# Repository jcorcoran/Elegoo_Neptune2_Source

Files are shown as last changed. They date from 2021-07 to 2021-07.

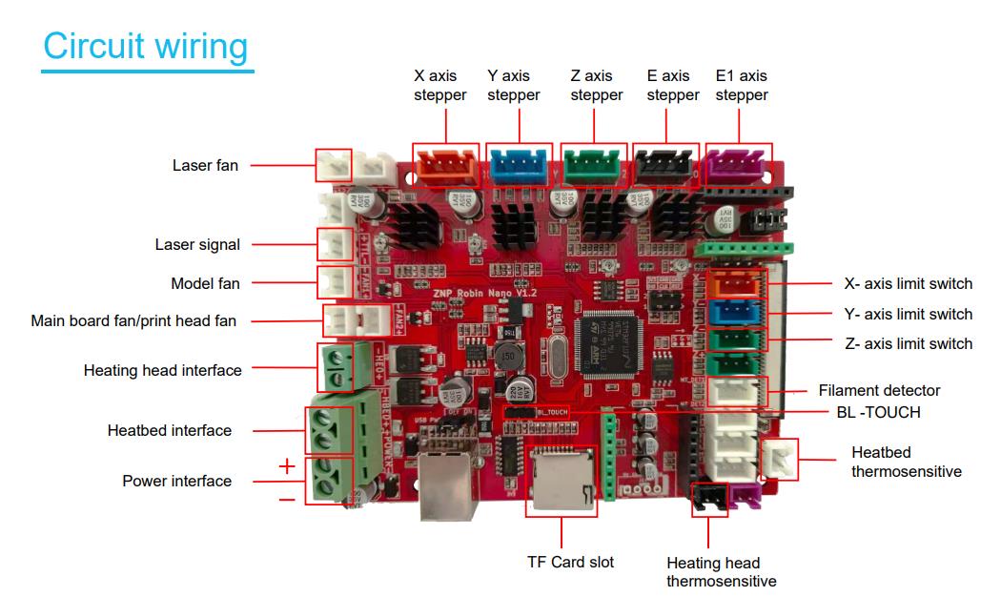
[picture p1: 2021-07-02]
PCBA/CIRCUIT WIRING.jpg

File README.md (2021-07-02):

# Elegoo_Neptune2_Source
Firmware, Shematics, BOM for the Elegoo Neptune2

This repo is a copy of the Elegoo Neptune 2 Source rar file hosted on the
[manufacturers web page](https://www.elegoo.com/pages/3d-printing-user-support) (downloaded 07/01/2021).  

Mirroring here for convenience of having the unpacked archive avaialble, and in the event it goes away/changes.

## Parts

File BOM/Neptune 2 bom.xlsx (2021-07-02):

Neptune 2 BOM
Order | Part Code | Part Name | Specification | UNIT | Qty
1 | 01.001.0001 | 2020 Aluminum profile_X-axis | 20*20-L345mm | pcs | 1.00
2 | 01.001.0002 | 2020 Aluminum profile_Top | 20*20-L330mm | pcs | 1.00
3 | 01.002.0001 | 2040 Aluminum profile_Right | 20*40-L400mm | pcs | 1.00
4 | 01.002.0002 | 2040 Aluminum profile_Left | 20*40-L400mm | pcs | 1.00
5 | 01.003.0001 | 4040 Aluminum profile_Y-axis | 40*40-L345mm | pcs | 1.00
6 | 01.003.0002 | 4040 Aluminum profile_Bottom & Right | 40*40-L290mm | pcs | 1.00
7 | 01.003.0003 | 4040 Aluminum profile_Bottom & Left | 40*40-L290mm | pcs | 1.00
8 | 01.003.0004 | 4040 Aluminum profile_Bottom | 40*40-L250mm | pcs | 1.00
9 | 02.001.0001 | Fixing Plate_Extruder | 2.5mm Aluminum alloy plate_AL5052 | pcs | 1.00
10 | 02.001.0002 | Fixing Plate_X-axis Motor | 3mm Aluminum alloy plate_AL5052 | pcs | 1.00
11 | 02.001.0003 | Driven Plate_X-axis | 2mm Aluminum alloy plate_AL5052 | pcs | 1.00
12 | 02.001.0001 | Driven Plate_Y-axis | SPCC t=2.0mm | pcs | 1.00
13 | 02.001.0004 | Fixing Plate_Y-axis Motor | 2.5mm Aluminum alloy plate_AL5052 | pcs | 1.00
14 | 02.001.0005 | Driven Plate_Z-axis | 3mm Aluminum alloy plate_AL5052 | pcs | 1.00
15 | 02.001.0006 | Fixing Plate_Nozzle Kit | 2.5mm Aluminum alloy plate_AL5052 | pcs | 1.00
16 | 02.001.0007 | Bottom Slider Plate | 4mm Aluminum alloy plate_AL5052 | pcs | 1.00
17 | 07.006.0001 | Thermistor_Heated Bed | D1.8mm_L700mm_100K | pcs | 1.00
18 | 07.006.0002 | Thermistor_Nozzle Kit | D1.8mm_L1300mm_100K | pcs | 1.00
19 | 07.007.0001 | Heating Tube | 24V_40W_L1400mm_Φ6mm*20mm | pcs | 1.00
20 | 07.005.0001 | 5015 Turbo Fan | 24V_5015_L120mm_Turbo Fan | pcs | 1.00
21 | 07.005.0002 | 4010 Turbo Fan | 24V_4010_L1310mm_Turbo Fan | pcs | 1.00
22 | 07.005.0003 | 4010 Axial Fan | 24V_4010_L1300mm_Axial Fan | pcs | 1.00
23 | 04.001.0001 | Yellew Earth Wire | 18AWG_L170mm_4.0 U-terminal+4.8 Plug spring terminal | pcs | 1.00
24 | 04.001.0002 | Black Silicone Wire | 16AWG_L170mm_4.0 U-terminal+4.8 Plug spring terminal | pcs | 1.00
25 | 04.002.0001 | Heated Bed Wire | 16AWG_L600mm_Strip 6mm at both ends and add tin | pcs | 1.00
26 | 04.001.0003 | Red Silicone Wire_Combined Switch | 16AWG_L90mm_4.8 Plug spring terminal(Both sides) | pcs | 1.00
27 | 04.003.0001 | Red And Black Wire_Mainboard | 16AWG_L410mm_Amass XT60 female terminal+Strip 5mm and add tin | pcs | 1.00
28 | 04.004.0001 | Red And Black Wire_Power Supply | 16AWG-L200mm_Amass XT60 male terminal+4.0 U-terminal | pcs | 1.00
29 | 04.005.0001 | Motor and limit switch wire_Y-axis | L380mm | pcs | 1.00
30 | 04.005.0002 | Motor and limit switch wire_Z-axis | Motor-L250mm_Limit switch-L290mm | pcs | 1.00
31 | 04.001.0004 | Red Silicone Wire_Combined Switch | 16AWG_L170mm_4.0 U-terminal+4.8 Plug spring terminal | pcs | 1.00
32 | 04.005.0003 | Motor and limit switch wire_X/E-axis | E-axis Motor-L810mm_X-axis Motor-L860mm_X-axis limit switch-L910mm | pcs | 1.00
33 | 04.006.0001 | Filament Detector Wire | L880mm | pcs | 1.00
34 | 05.001.0001 | Plastic Bottom Box | Black_ABS765A Fireproof materials_Fire ratingV-0 | pcs | 1.00
35 | 05.001.0002 | Plastic Bottom Cover | Black_ABS765A Fireproof materials_Fire ratingV-0 | pcs | 1.00
36 | 05.001.0003 | Screen Fixing Bracket | Black_ABS765A Fireproof materials_Fire ratingV-0 | pcs | 1.00
37 | 05.001.0004 | Fan Cover | Black_ABS765A Fireproof materials_Fire ratingV-0 | pcs | 1.00
38 | 05.001.0005 | Power Supply Fixing Box | Black_ABS765A Fireproof materials_Fire ratingV-0 | pcs | 1.00
39 | 05.001.0006 | Fixed Seat_Heated Bed Wire | Black_ABS765A Fireproof materials_Fire ratingV-0 | pcs | 1.00
40 | 05.001.0007 | Fixed Seat Cover_Heated Bed Wire | Black_ABS765A Fireproof materials_Fire ratingV-0 | pcs | 1.00
41 | 05.001.0008 | Fixed Seat_Filament Detector Switch | Black_ABS765A Fireproof materials_Fire ratingV-0 | pcs | 1.00
42 | 05.001.0009 | Extruder Base | Black_ABS765A+PC Fireproof materials_Fire ratingV-0 | pcs | 1.00
43 | 05.001.0010 | Extruder Handle | Black_ABS765A+PC Fireproof materials_Fire ratingV-0 | pcs | 1.00
44 | 05.001.0011 | Fixed Seat of Limit Switch_X-axis | Black_ABS765A Fireproof materials_Fire ratingV-0 | pcs | 1.00
45 | 05.001.0012 | Fixed Seat of Limit Switch_Z-axis | Black_ABS765A Fireproof materials_Fire ratingV-0 | pcs | 1.00
46 | 05.001.0015 | Fixed Seat of Limit Switch_Y-axis | Black_ABS765A Fireproof materials_Fire ratingV-0 | pcs | 1.00
47 | 05.001.0014 | Filament Holder | Black_ABS765A Fireproof materials_Fire ratingV-0 | pcs | 1.00
48 | 05.001.0015 | Filament Tube | Black_ABS765A+PC Fireproof materials_Fire ratingV-0 | pcs | 1.00
49 | 05.001.0016 | 4040 Profile Cover | Black_ABS765A Fireproof materials_Fire ratingV-0 | pcs | 4.00
50 | 05.001.0017 | 2020 Profile Cover | Black_ABS765A Fireproof materials_Fire ratingV-0 | pcs | 2.00
51 | 05.001.0018 | Hand Screw Nut | Black_ABS765A Fireproof materials_Fire ratingV-0 | pcs | 4.00
52 | 05.001.0019 | Fixed Seat of Stepper_Z-axis | Black_ABS765A Fireproof materials_Fire ratingV-0 | pcs | 1.00
53 | 05.001.0020 | Silicone Cover | Silica Gel_Black | pcs | 1.00
54 | 05.001.0021 | Clamp of Pneumatic Fittings | φ5.7mm Blue | pcs | 3.00
55 | 08.001.0001 | Neptune 2 Mainboard | Elegoo ZNP Robin Nano V1.2 | pcs | 1.00
56 | 08.002.0001 | Neptune 2 Display Screen | Elegoo ZNP Robin TFT35 V1.0 | pcs | 1.00
57 | 04.007.0001 | FFC Cable | FFC Cable_L300mm_32P_Distance 1.0mm_Same side | pcs | 1.00
58 | 07.003.0001 | Limit Switch | With PCBA | pcs | 3.00
59 | 07.003.0002 | Filament Detector Switch | With PCBA | pcs | 1.00
60 | 07.002.0004 | 42-34 Stepper_Black（Flat shaft） | 42HD2037-02_Two-phase_Black | pcs | 2.00
61 | 07.002.0005 | 42-34 Stepper_Black（Circular Axis） | 42HD2037-04_Two-phase_Black | pcs | 1.00
62 | 07.002.0006 | 42-40 Stepper_Black | 42HD4027-02_Two-phase_Black | pcs | 1.00
63 | 07.001.0001 | Power Supply_Black | 24V_15A | pcs | 1.00
64 | 07.003.0003 | Combination Switch | Three-in-one combination switch | pcs | 1.00
65 | 08.003.0001 | Fuse | 10A_250V_5mm*20mm | pcs | 1.00
66 | 07.004.0001 | Heated Bed Platform | 24V_235mm*235mm_220W | pcs | 1.00
67 | 03.002.0001 | Heating Block | 20mm*20mm*10mm | pcs | 1.00
68 | 03.003.0001 | Heat Dissipation Block | 12mm*20mm*27.8mm_2*M3 | pcs | 1.00
69 | 03.004.0001 | Nozzle | 0.4mm | pcs | 2.00
70 | 03.005.0001 | Throat Tube | D7mm_M6_L27mm_through | pcs | 1.00
71 | 03.007.0001 | V-slot Wheel | Black_Imported POM_Size：24*10mm | pcs | 13.00
72 | 03.006.0001 | Metal Eccentric Spacer | D7.2mm_d5mm_H8.35mm_Outer Hexagon | pcs | 5.00
73 | 03.006.0002 | Metal Spacer | D8mm_d5mm_H8.35mm | pcs | 11.00
74 | 03.001.0001 | Extrusion Gear | D11mm_40teeth_Copper | pcs | 1.00
75 | 06.004.0001 | Compression Spring_Heated Bed | φ0.9mm*φ8mm*L20mm | pcs | 4.00
76 | 06.004.0002 | Compression Spring_Nozzle Kit | φ1.1mm*φ8mm*L22mm | pcs | 1.00
77 | 06.001.0001 | Ball bearing_U-624 | U-624 | pcs | 1.00
78 | 06.001.0002 | Ball bearing_F-624-ZZ | F-624-ZZ | pcs | 4.00
79 | 06.001.0003 | Ball bearing_625-ZZ | 625-ZZ | pcs | 26.00
80 | 06.003.0001 | Lead Screws_T8 | T8-8_L355mm | pcs | 1.00
81 | 06.003.0002 | Lead Screws Nut_T8 | T8-8 | pcs | 1.00
82 | 06.007.0001 | Rigid Coupling | D5mm*8mm | pcs | 1.00
83 | 06.009.0001 | Pneumatic Fittings | PC4-1/8PT | pcs | 3.00
84 | 06.006.0001 | Timing Pulley | 2GT_d5mm_20teeth_W6mm | pcs | 2.00
85 | 05.002.0001 | Timing Belt | 2GT-W6_X-axis 780mm_Y-axis 750mm | m | 1.53
86 | 06.009.0002 | Copper Sleeve_Timing Belt | D7mm_0.5mm | pcs | 4.00
87 | 05.003.0001 | Nylon Column Ⅰ | φ7mm-φ4.2mm-H15mm | pcs | 2.00
88 | 05.003.0002 | Nylon Column Ⅱ | φ7mm-φ4.2mm-H8mm | pcs | 2.00
89 | 10.006.0001 | Platform Sticker | 235mm*235mm | pcs | 1.00
90 | 05.006.0001 | Glass Fiber Platform | 235mm*235mm | pcs | 1.00
91 | 10.005.0001 | Rubber Mat | 20*40mm_H3mm | pcs | 4.00
92 | 05.007.0001 | Teflon Tube | D4-d2_white_L380mm | m | 0.38
93 | 10.001.0001 | Nylon braided sleeve Ⅰ | W8mm_L410mm | pcs | 1.00
94 | 10.001.0004 | Nylon braided sleeve Ⅱ | W8mm_L700mm | pcs | 1.00
95 | 10.001.0003 | Nylon braided sleeve Ⅲ | W12mm_L650mm | pcs | 1.00
96 | 11.003.0001 | Insulation Cotton | 50mm*60mm | pcs | 1.00
97 | 10.008.0001 | Long Tail Clip | 6#_15mm | pcs | 4.00
98 | 10.007.0004 | Cable Tie 4-150 | Black_4*150mm | pcs | 15.00
99 | 10.007.0005 | Fixed Head Cable Tie 3-100 | Black_3*100mm | pcs | 2.00
100 | 11.002.0003 | High Temperature Insulating Polyimide Tape Ⅰ | W10mm | m | 0.08
101 | 11.002.0002 | High Temperature Insulating Polyimide Tape Ⅱ | W50mm | m | 0.20
102 | 11.001.0001 | High Temp Resistant Thread Sealant | 272_Red_High Temp Resistant | g | 0.50
103 | 11.004.0001 | Grease | Transparent_Paste | g | 2.00
104 | 11.004.0002 | Thermal Grease | Grey | g | 0.20
105 | 10.004.0001 | TF Memory Card | 8G | pcs | 1.00
106 | 10.004.0002 | TF Memory Card Reader | CHUANYU（Common） | pcs | 1.00
107 | 04.008.0005 | Power Supply | Length:1.5M_Wire diameter:6.5mm_Rated power:2500W_Rated voltage:250V_Pure copper_3*0.75mm²_Plug:nickel-plated brass_Flame-Retardant PVC | pcs | 1.00
108 | 04.009.0001 | USB Cable | Bluish transparent_Type-A to Type-B_Length:53cm_Wire diameter:4.8mm | pcs | 1.00
109 | 10.008.0002 | Needle | Stainless Steel_L70mm_d0.35mm | pcs | 1.00
110 | 10.002.0001 | Metal Scraper | Stainless Steel_1.5#_Nickel-plated | pcs | 1.00
111 | 10.002.0002 | Nippers | Cutting Nippers | pcs | 1.00
112 | 10.002.0003 | 1.5mm Inner Hexagon Spanner | Carbon Steel_1.5mm_Nickel-plated | pcs | 1.00
113 | 10.002.0004 | 2.0mm Inner Hexagon Spanner | Carbon Steel_2.0mm_Nickel-plated | pcs | 1.00
114 | 10.002.0005 | 2.5mm Inner Hexagon Spanner | Carbon Steel_2.5mm_Nickel-plated | pcs | 1.00
115 | 10.002.0006 | 3.0mm Inner Hexagon Spanner | Carbon Steel_3.0mm_Nickel-plated | pcs | 1.00
116 | 10.002.0007 | 4.0mm Inner Hexagon Spanner | Carbon Steel_4.0mm_Nickel-plated | pcs | 1.00
117 | 10.002.0008 | Flat Blade Screwdriver | 2.5mm_Flat Blade | pcs | 1.00
118 | 10.002.0009 | Cruciform Screwdriver | 4.0mm_ Cruciform | pcs | 1.00
119 | 10.002.0010 | Double Open Spanner | 45#steel_8-10#_Galvanized | pcs | 1.00
120 | 10.002.0011 | Open Spanner | 45#steel_6#_Galvanized | pcs | 1.00
121 | 12.002.0005 | Lead Screws Sleeve | PE_30mm*370mm_Single side Thickness:0.1mm | pcs | 1.00
122 | 12.002.0001 | Self Sealing Bag Ⅰ | 18cm*26cm_Thickness:0.06mm | pcs | 1.00
123 | 12.002.0002 | Self Sealing Bag Ⅱ | 15cm*20cm_Thickness:0.08mm | pcs | 2.00
124 | 12.002.0003 | Self Sealing Bag Ⅲ | 9cm*13cm_Thickness:0.08mm | pcs | 3.00
125 | 12.002.0004 | Self Sealing Bag Ⅳ | 6cm*9cm_Thickness:0.08mm | pcs | 2.00
126 | 13.001.0001 | Filament | L5m_Random color | pcs | 1.00
127 | 10.003.0001 | Product Certificate | Triangle | pcs | 1.00
128 | 12.003.0001 | Neptune 2 Foam |  | pcs | 1.00
129 | 12.001.0001 | Neptune 2 Carton |  | pcs | 1.00
130 | 10.003.0003 | Neptune 2 User Guide |  | pcs | 1.00
131 | 12.004.0001 | Neptune 2 Manufacturing Number Sticker |  | pcs | 1.00
132 | 12.004.0002 | Neptune 2 Machine Specification Sticker |  | pcs | 1.00
133 | 10.007.0003 | Plastic Twist Tie | White_Plastic Twist Tie_0.55mm*80mm | pcs | 1.00
134 | 12.005.0001 | Heated Bed Warning Sticker | 80G_Coated Paper | pcs | 1.00
135 | 09.001.0001 | Hexagon Socket Countersunk Head Screw_M3*18 | Stainless Steel_M3*18 | pcs | 4.00
136 | 09.001.0002 | Hexagon Socket Countersunk Head Screw_M3*10 | Stainless Steel_M3*10 | pcs | 1.00
137 | 09.001.0003 | Hexagon Socket Countersunk Head Screw_M4*20 | Carbon Steel_M4*20 | pcs | 2.00
138 | 09.001.0004 | Cross Recessed Countersunk Head Screw_M4*35 | Stainless Steel_M4*35 | pcs | 4.00
139 | 09.002.0001 | Hexagon Socket Button Head Screw_M3*6 | Stainless Steel_M3*6 | pcs | 12.00
140 | 09.002.0002 | Hexagon Socket Button Head Screw_M3*16 | Stainless Steel_M3*16 | pcs | 4.00
141 | 09.002.0003 | Hexagon Socket Button Head Screw_M5*30 | Stainless Steel_M5*30 | pcs | 10.00
142 | 09.002.0004 | Hexagon Socket Button Head Screw_M3*10 | Stainless Steel_M3*10 | pcs | 4.00
143 | 09.002.0005 | Hexagon Socket Button Head Screw_M5*40 | Stainless Steel_M5*40 | pcs | 3.00
144 | 09.002.0006 | Hexagon Socket Button Head Screw_M5*8 | Stainless Steel_M5*8 | pcs | 4.00
145 | 09.002.0007 | Hexagon Socket Button Head Screw_M4*16 | Stainless Steel_M4*16 | pcs | 6.00
146 | 09.002.0008 | Hexagon Socket Button Head Screw_M4*6 | Carbon Steel_M4*6 | pcs | 1.00
147 | 09.002.0009 | Hexagon Socket Button Head Screw_M3*12 | Stainless Steel_M3*12 | pcs | 2.00
148 | 09.003.0001 | Hexagon Socket Head Cap Screw_M4*8 | Stainless Steel_M4*8 | pcs | 10.00
149 | 09.003.0002 | Hexagon Socket Head Cap Screw_M3*18 | Stainless Steel_M3*18 | pcs | 1.00
150 | 09.003.0003 | Hexagon Socket Head Cap Screw_M4*35 | Stainless Steel_M4*35 | pcs | 1.00
151 | 09.003.0004 | Hexagon Socket Head Cap Screw_M4*18 | Stainless Steel_M4*18 | pcs | 2.00
152 | 09.003.0005 | Hexagon Socket Head Cap Screw_M4*20 | Stainless Steel_M4*20 | pcs | 2.00
153 | 09.003.0006 | Hexagon Socket Head Cap Screw_M4*50 | Stainless Steel_M4*50 | pcs | 1.00
154 | 09.003.0007 | Hexagon Socket Head Cap Screw_M4*10 | Stainless Steel_M4*10 | pcs | 2.00
155 | 09.004.0001 | M5 Flat Washer_V-slot Wheel | M5_φ5mm*φ8mm*1mm | pcs | 13.00
156 | 09.004.0002 | M3 Spring Washer | Stainless Steel_M3 | pcs | 4.00
157 | 09.004.0003 | M5 Flat Washer | Stainless Steel_M5 | pcs | 5.00
158 | 09.004.0004 | M4 Spring Washer | Stainless Steel_M4 | pcs | 2.00
159 | 09.005.0001 | M4 T-nut | Stainless Steel_M4 | pcs | 8.00
160 | 09.005.0002 | M5 Self-locking Nut | Stainless Steel_M5 | pcs | 13.00
161 | 09.005.0003 | 4 Self-locking Nut | Stainless Steel_M4 | pcs | 1.00
162 | 09.005.0004 | Self-locking Nut | Stainless Steel_M3 | pcs | 2.00
163 | 09.006.0001 | Pan Head Tapping Screws_Point Tail_3*14 | Stainless Steel_PA 3*14 | pcs | 2.00
164 | 09.006.0002 | Pan Head Tapping Screws_Point Tail_3*12 | Stainless Steel_PA 3*12 | pcs | 8.00
165 | 09.006.0003 | Pan Head Tapping Screws_Point Tail_3*8 | Stainless Steel_PA 3*8 | pcs | 15.00
166 | 09.006.0004 | Pan Head Tapping Screws_Point Tail_3*20 | Stainless Steel_PA 3*20 | pcs | 2.00
167 | 09.007.0001 | Combination Screw_M3*4 | Stainless Steel_M3*4 | pcs | 1.00
168 | 09.007.0002 | Combination Screw with Spring washer_M4*18 | Carbon Steel_M4*18 | pcs | 4.00
169 | 09.007.0003 | Combination Screw with Spring washer_M5*25 | Carbon Steel_M5*25 | pcs | 4.00
170 | 09.007.0004 | Combination Screw with Spring washer_M5*45 | Carbon Steel_M5*45 | pcs | 10.00
171 | 09.008.0001 | Set Screw_M3*3 | Carbon Steel_M3*3 | pcs | 4.00

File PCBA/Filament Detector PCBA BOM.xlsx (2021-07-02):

序号 | 名称 | 规格 | 数量 | 单位
1 | PCB |  | 1 | pcs
2 | 贴片电容 | 100nF | 2 | pcs
3 | 贴片电阻 | 0Ω | 1 | pcs
4 | 贴片电阻 | 510Ω | 1 | pcs
5 | 发光二极管 0603 | 蓝色 | 1 | pcs
6 | 微动开关 |  | 1 | pcs
7 | 接线端子 | 2.54-3P | 1 | pcs

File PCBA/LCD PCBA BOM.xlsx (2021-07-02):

序号 | 名称 | 规格 | 数量 | 单位
1 | PCB |  | 1 | pcs
2 | 贴片电容 | 100nF | 4 | pcs
3 | 贴片电容 | 10nF | 2 | pcs
4 | 贴片电容 | 4.7uF | 2 | pcs
5 | 贴片电阻 | 1KΩ | 4 | pcs
6 | 贴片电阻 | 10KΩ | 3 | pcs
7 | 集成电阻 | 47Ω | 1 | pcs
8 | IC TSC2046I | TSSOP-16 | 1 | pcs
9 | 蜂鸣器 |  | 1 | pcs
10 | 三极管 | BC817 | 1 | pcs
11 | 三极管 | BCW66 | 1 | pcs
12 | 贴片连接器下接 | FPC-32pin-1.0mm | 1 | pcs
13 | 贴片连接器抽屉上接 | FPC-40pin-0.5mm | 1 | pcs
14 | 显示屏带触摸屏 |  | 1 | pcs
15 | 显示屏框 | 3.5吋黑色 | 1 | pcs

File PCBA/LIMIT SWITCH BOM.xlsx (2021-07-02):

序号 | 名称 | 规格 | 数量 | 单位
1 | PCB |  | 1 | pcs
2 | 微动开关 |  | 1 | pcs
3 | 接线端子 | 2.54-3P | 1 | pcs
4 | 盘头自攻螺丝 |  | 2 | pcs

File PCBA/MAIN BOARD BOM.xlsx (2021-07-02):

序号 | 名称 | 规格 | 数量 | 单位
1 | PCB |  | 1 | pcs
2 | C0603 | 100nF | 41 | pcs
3 | C0603 | 22pF | 2 | pcs
4 | C0603 | 22nF | 2 | pcs
5 | C0603 | 220nF | 2 | pcs
6 | C0603 | 150pF | 1 | pcs
7 | C0603 | 1uF | 1 | pcs
8 | C0805 | 10uF | 2 | pcs
9 | 贴片铝电解电容 | 10uF | 3 | pcs
10 | 贴片铝电解电容 | 100uF | 7 | pcs
11 | 贴片铝电解电容 | 220uF | 1 | pcs
12 | 电阻0603 | 4.7KΩ | 18 | pcs
13 | 电阻0603 | 10KΩ | 18 | pcs
14 | 电阻0603 | 0Ω | 10 | pcs
15 | 电阻0603 | 1KΩ | 10 | pcs
16 | 电阻0603 | 20KΩ | 10 | pcs
17 | 电阻0603 | 100Ω | 5 | pcs
18 | 电阻0603 | 100KΩ | 4 | pcs
19 | 电阻0603 | 22Ω | 2 | pcs
20 | 电阻0603 | 1MΩ | 1 | pcs
21 | 电阻0603 | 210KΩ | 1 | pcs
22 | 电阻0603 | 40.2KΩ | 1 | pcs
23 | 电阻0603 | 24.9K | 1 | pcs
24 | 电阻0603 | 1.8KΩ | 3 | pcs
25 | 电阻0805 | 0.11Ω | 4 | pcs
26 | 电阻0805 | 0.1Ω | 4 | pcs
27 | 电阻0805 | 10Ω | 1 | pcs
28 | 可调电位器 | 20KΩ | 2 | pcs
29 | 贴片电感 | 15uH | 1 | pcs
30 | L0805 | BLM21PG221SN1D | 1 | pcs
31 | 整流二级管 | S1G | 1 | pcs
32 | 整流二级管 | S1A | 1 | pcs
33 | 二极管 | B340A | 1 | pcs
34 | 整流二极管 | SS12A | 1 | pcs
35 | 发光二极管 0603 | 红色 | 5 | pcs
36 | 发光二极管 0603 | 绿色 | 2 | pcs
37 | TMC2225 | TMC2225 | 2 | pcs
38 | STM32F103VET6 | LQFP100 | 1 | pcs
39 | A4988 | A4988 | 2 | pcs
40 | IC AT24C16N | SOIC-8 | 1 | pcs
41 | IC MP1584EN | SOIC-8 | 1 | pcs
42 | IC CH340C | SOP | 1 | pcs
43 | IC NCP1117ST33T3G | SOT | 1 | pcs
44 | IC W25Q64JVSSIQ | SOIC | 1 | pcs
45 | 晶振8M-20pF | DIP | 1 | pcs
46 | 保险丝-3216FF | 30A | 1 | pcs
47 | 保险丝-3216FF | 15A | 1 | pcs
48 | 自恢复保险丝 | MSMD15 | 1 | pcs
49 | 自恢复保险丝 | MSMD050 | 1 | pcs
50 | 贴片连接器下接 | FPC-32pin-1.0mm | 1 | pcs
51 | Micro SD镀金卡座 |  | 1 | pcs
52 | 集成电阻 | 100Ω | 5 | pcs
53 | 集成电阻 | 10Ω | 1 | pcs
54 | 集成电阻 | 4.7KΩ | 1 | pcs
55 | 集成电阻 | 100KΩ | 1 | pcs
56 | 压敏电阻 | 05E | 3 | pcs
57 | NMOS管 | AO3400 | 2 | pcs
58 | 贴片可调电位器 | 10KΩ | 2 | pcs
59 | MOS管 | HY1403D | 1 | pcs
60 | MOS管 | HY3403D | 1 | pcs
61 | 插座 2.54 | M8x1黑色 | 2 | pcs
62 | 插座 2.54 | M8x1绿色 | 2 | pcs
63 | 螺钉式接线端子 5.0-2P | 绿色 | 1 | pcs
64 | 插针 2.54 | M3x1 直脚 | 2 | pcs
65 | 插针 2.54 | M4x1 直脚 | 1 | pcs
66 | 插针 2.54 | M6x1 直脚 | 1 | pcs
67 | 插针 2.54 | M3x2 直脚 | 2 | pcs
68 | 螺钉式接线端子 | 5.00-4P 绿色短脚（HG129） | 1 | pcs
69 | USB连接器-USB-B_TH | USB | 1 | pcs
70 | 接线端子 | 2.54-2P 白色 | 8 | pcs
71 | 接线端子 | 2.54-2P 黑色 | 1 | pcs
72 | 接线端子 | 2.54-2P 紫色 | 1 | pcs
73 | 接线端子 | 2.54-3P 白色 | 4 | pcs
74 | 接线端子 | 2.54-3P 红色 | 1 | pcs
75 | 接线端子 | 2.54-3P 蓝色 | 1 | pcs
76 | 接线端子 | 2.54-3P 绿色 | 2 | pcs
77 | 接线端子 | 2.54-4P 红色 | 1 | pcs
78 | 接线端子 | 2.54-4P 蓝色 | 1 | pcs
79 | 接线端子 | 2.54-4P 绿色 | 1 | pcs
80 | 接线端子 | 2.54-4P 黑色 | 1 | pcs
81 | 接线端子 | 2.54-4P 紫色 | 1 | pcs
82 | 短路帽 | 2.54 | 4 | pcs

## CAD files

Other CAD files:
Wire/Red And Black Wire_Mainboard.dwg
2D/4040 Aluminum profile_Bottom.DWG
3D/Neptune 2.STEP
Wire/Thermistor_Nozzle Kit.dwg
2D/2020 Aluminum profile_Top.DWG
Wire/5015 Turbo Fan.dwg
2D/Metal Eccentric Spacer.DWG
Wire/Thermistor_Heated Bed.dwg
2D/Bottom Slider Plate.DWG
Wire/motor and limit switch wire_XE-axis.dwg
2D/Plastic Bottom Cover.DWG
Wire/4010 Axial Fan.dwg
2D/Fan Cover.DWG
2D/Heat Dissipation Block.DWG
Wire/4010 Turbo Fan.dwg
2D/4040 Aluminum profile_Y-axis.DWG
Wire/Yellew Earth Wire.dwg
2D/Throat Tube.DWG
2D/2020 Aluminum profile_X-axis.DWG
2D/2020 Profile Cover.DWG
2D/2040 Aluminum profile_Left.DWG
2D/4040 Aluminum profile_Bottom & Left.DWG
2D/4040 Aluminum profile_Bottom & Right.DWG
2D/4040 Profile Cover.DWG
2D/Driven Plate_X-axis.DWG
2D/Driven Plate_Y-axis.DWG
2D/Driven Plate_Z-axis.DWG
2D/Extruder Base.DWG
2D/Extruder Handle.DWG
2D/Filament Holder.DWG
2D/Filament Tube.DWG
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

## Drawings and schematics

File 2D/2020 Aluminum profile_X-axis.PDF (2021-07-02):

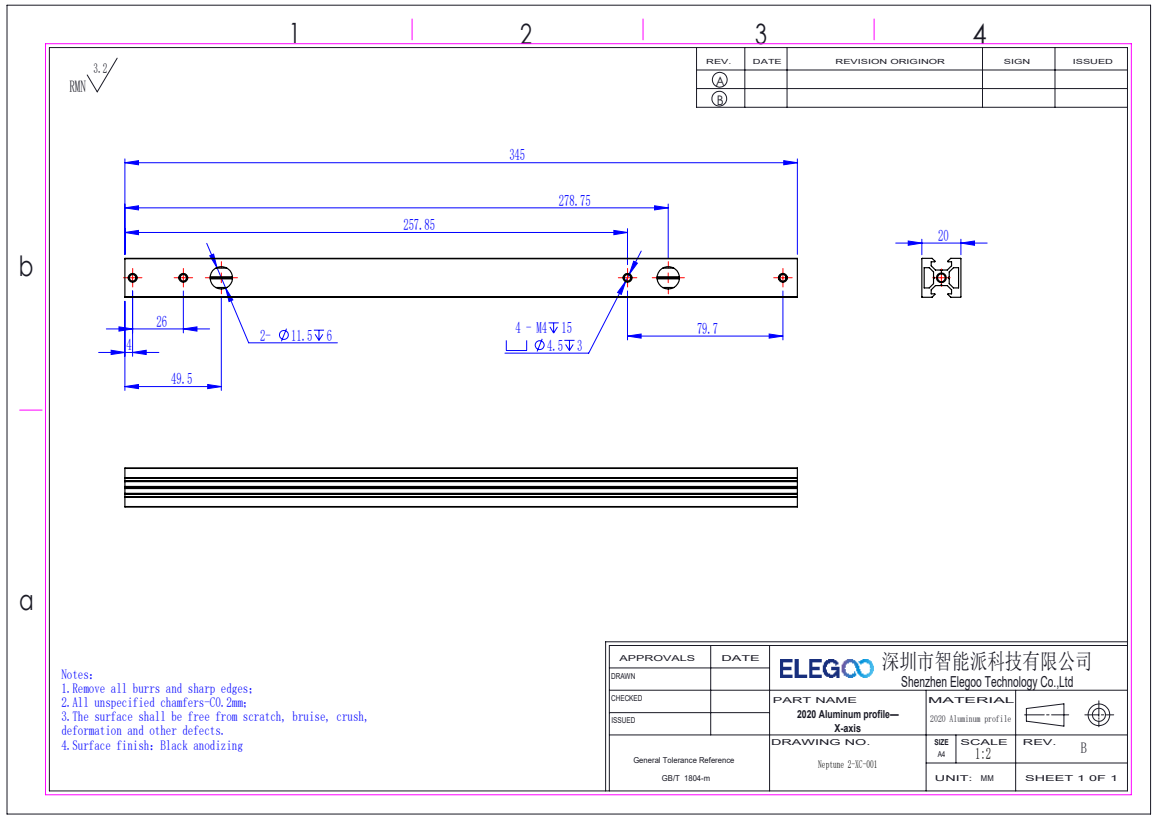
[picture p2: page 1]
Neptune 2-XC-001; SIZE SCALE; UNIT: MM; DRAWING NO.; REV.; DATE; REVISION ORIGINOR; SIGN; ISSUED; SHEET 1 0F 1

深圳市智能派科技有限公司
Shenzhen Elegoo Technology Co.,Ltd

Notes：
1.Remove all burrs and sharp edges；
2.All unspecified chamfers-C0.2mm；
3.The surface shall be free from scratch, bruise, crush,
deformation and other defects.
4.Surface finish：Black anodizing

PART NAME
2020 Aluminum profile 2020 Aluminum profile—
X-axis

General Tolerance Reference

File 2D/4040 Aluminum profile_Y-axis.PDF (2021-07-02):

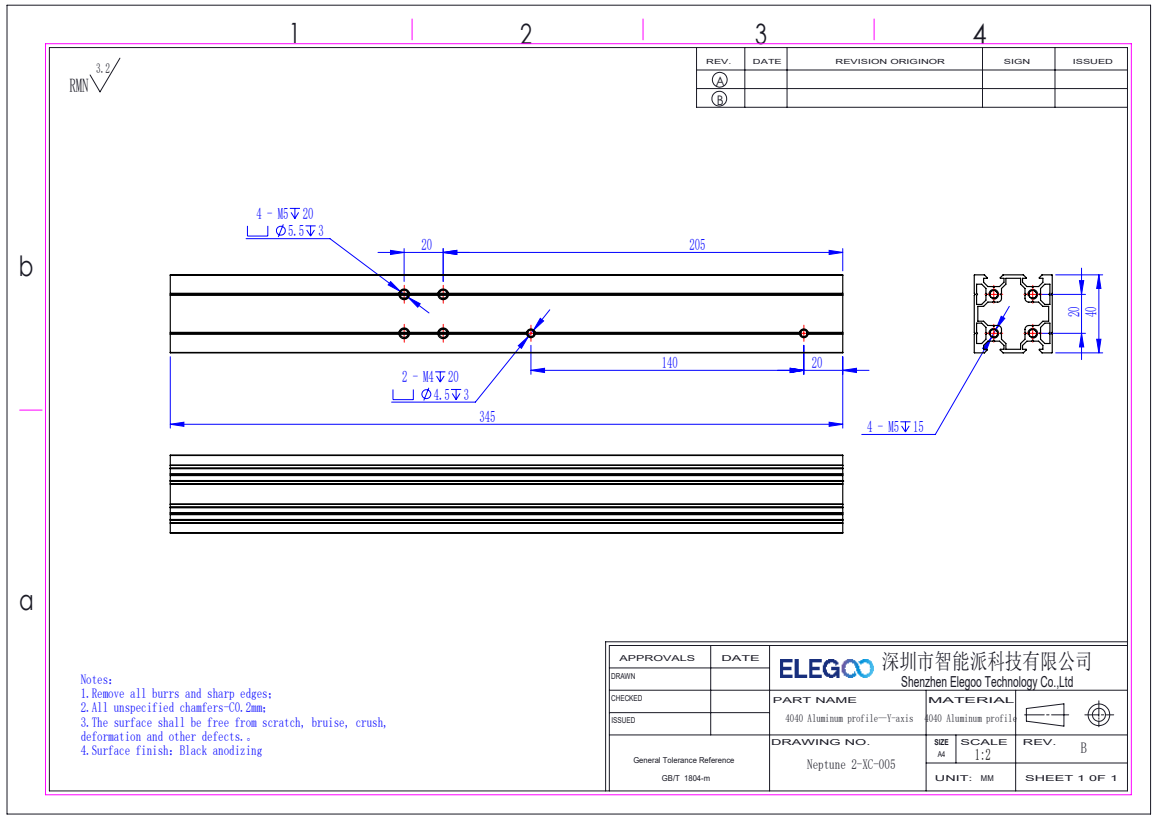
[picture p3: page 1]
4040 Aluminum profile; Neptune 2-XC-005; 4.Surface finish：Black anodizing; SIZE SCALE; UNIT: MM; DRAWING NO.; REV.; DATE; REVISION ORIGINOR; SIGN; ISSUED; SHEET 1 0F 1

深圳市智能派科技有限公司
Shenzhen Elegoo Technology Co.,Ltd

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

PART NAME
4040 Aluminum profile—Y-axis

General Tolerance Reference

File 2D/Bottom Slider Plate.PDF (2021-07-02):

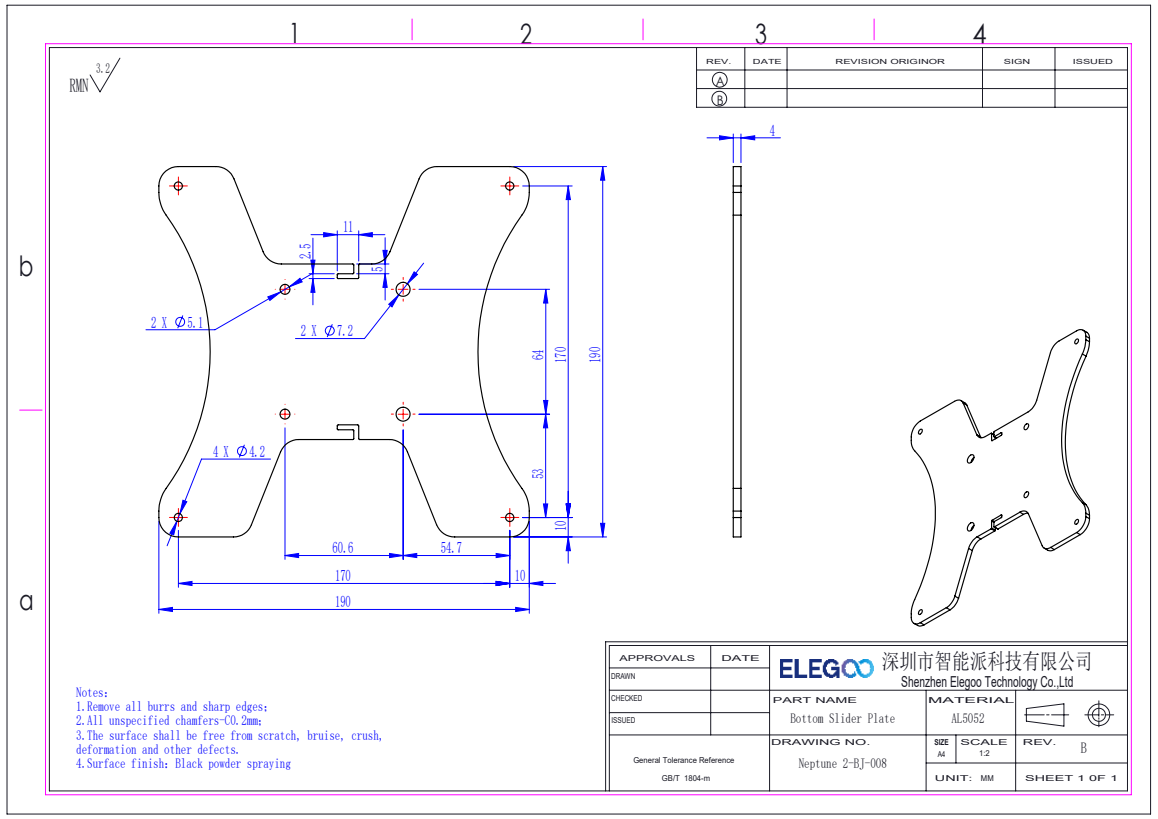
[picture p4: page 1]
Bottom Slider Plate; Neptune 2-BJ-008; 4.Surface finish：Black powder spraying; SIZE SCALE; UNIT: MM; DRAWING NO.; REV.; DATE; REVISION ORIGINOR; SIGN; ISSUED; PART NAME; SHEET 1 0F 1

深圳市智能派科技有限公司
Shenzhen Elegoo Technology Co.,Ltd

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

General Tolerance Reference
